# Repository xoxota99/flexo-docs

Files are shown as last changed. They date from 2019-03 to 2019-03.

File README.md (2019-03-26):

# flexo-docs

<table><tr><td width="100"></td><td>
Flexo is a 6DOF robot arm using stepper motors instead of (e.g.) servos. <br/>
This project is the documentation repository for Flexo. It includes CAD files, assembly instructions, inverse kinematics solver in Excel, datasheets, BOM, schematics, and othe miscellany that don't quite qualify as "source code".
</td></tr></table>

## See also:
<ul>
  <li><a href="https://github.com/xoxota99/flexo-server">flexo-server</a> - for documentation</li>
  <li><a href="https://github.com/xoxota99/flexo-controller">flexo-controller</a> - for Arduino code</li></li>
</ul>

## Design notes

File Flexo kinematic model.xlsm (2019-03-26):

FORWARD KINAMATICS |  |  |  |  |  |  |  |  |  | INVERSE KINAMATICS
 | IN |  |  |  |  |  | OUT |  |  |  | IN
 | degrees | radians
J1 * ( -170 / 170 ) | 0.0001 | 1.745329252e-06 |  |  |  | X | 68.71814224 |  |  | X | 68.71814224 | J1 | 9.999999996e-05
J2 * ( -132 / 0 ) | -90 | -1.570796327 |  |  |  | Y | 0.0001199357837 |  |  | Y | 0.0001199357837 | J2 | -90
J3 * ( 1 / 140 ) | 1 | -1.553343034 |  |  |  | Z | 733.6105702 |  |  | Z | 733.6105702 | J3 | 1
 | 0 | 0 |  |  |  | y | -90 | -1.570796327 |  | y | -90 | J4 | -3.113901077e-10 | -3.113901077e-10 | 180
 | 0.0001 | 1.745329252e-06 |  |  |  | p | 1.0001 | 0.01745503785 |  | p | 1.0001 | J5 | 9.999727019e-05 | 9.999727019e-05 | -9.999727019e-05 |  | WRIST CONF. | "F"
 | 0 | 3.141592654 |  |  |  | r | -90.0001 | -1.570798072 |  | r | -90.0001 | J6 | 3.113598268e-10 | 3.113598268e-10 | -180 |  | QUADRANT | 1
 | DH params
 | joint | Θ | α | d | a |  | WORK FRAME |  | TOOL FRAME | CALCULATE J1 ANGLE
 | 1 | 1.745329252e-06 | -1.570796327 | 169.77 | 64.2 | X | 0 | X | 0 | J1 ∠ | 1.745329251e-06 | 9.999999996e-05
 | 2 | -1.570796327 | 0 | 0 | 305 | Y | 0 | Y | 0
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

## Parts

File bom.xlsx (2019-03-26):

BILL OF MATERIALS
PRODUCT NAME | Flexo-XP | CONTACT INFO
APPROVED BY | Phil Desrosiers | philippe.desrosiers@gmail.com
APPROVAL DATE | 2019-03-26
PART COUNT | 144
TOTAL COST | $741.03
ITEM NUMBER | ASSEMBLY | PART | MBOM Qty | PBOM Qty | PBOM UNITS | IMAGE | CATEGORY | ASSEMBLY PHASE | STATUS | SOURCE / SUPPLIER | LINK TO SUPPORTING DOC | COMMENTS | UNIT COST | TOTAL PART COST | STATUS KEY
B-1 | Base | NEMA 23 76mm | 1 | 1 | ea |  | Motor |  |  | StepperOnline.com | https://www.omc-stepperonline.com/nema-23-stepper-motor/nema-23-bipolar-19nm-269ozin-28a-32v-57x57x76mm-4wires-%CF%866mm-shaft-23hs30-2804s1.html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 |  | $28.15 | $28.15 | NOT STARTED
B-2 | Base | Turntable ring bearing, 6" | 1 | 1 | ea |  | Bearing |  |  | Amazon.com | https://www.amazon.com/dp/B073NYZMKJ |  | $14.99 | $14.99 | IN REVIEW
B-3 | Base | 20T Mod 1 6mm Spur gear | 1 | 1 | ea |  | Gear |  |  | SPI-SD | https://shop.sdp-si.com/catalog/Product.aspx?id=A_1C_2MYK10018# |  | $7.70 | $7.70 | COMPLETE
B-4 | Base | Magnetic Encoder / Axial Magnet | 1 | 6 | ea |  | Electronics |  |  | DigiKey | https://www.digikey.com/product-detail/en/ams/AS5048A-TS_EK_AB/AS5048A-AB-1.0-ND/3188612 |  | $16.76 | $100.56 | IN PRODUCTION
B-5 | Base | M5x25mm Flat Hex screws | 2 | 1 | 50-pk |  | Fasteners |  |  | McMaster-Carr |  | Motor mount |  | $0.00
B-5 | Base | M5x25mm Button-head Hex screws | 2 | 1 | 50-pk |  | Fasteners |  |  | McMaster-Carr |  | Motor mount |  | $0.00
B-6 | Base | M8x30mm Button-head Hex screws | 4 | 1 | 50-pk |  | Fasteners |  |  | McMaster-Carr |  | Baseplate mount |  | $0.00
B-7 | Base | M5 NyLock nuts | 4 | 1 | 50-pk |  | Fasteners |  |  | McMaster-Carr |  | Motor mount |  | $0.00
B-8 | Base | M4x25mm Flat Hex screws | 8 | 1 | 50-pk |  | Fasteners |  |  | McMaster-Carr |  | Ring bearing mount |  | $0.00
BX-1 | Base | 3D-printed Housing | 1 | 1 | ea |  | 3DPrint |  |  | Internal |  |  |  | $0.00
 | Base Total |  | 25 | 15 |  |  |  |  |  |  |  |  |  | $151.40
S-1 | Shoulder | NEMA-23 47:1 Geared Motor | 1 | 2 | ea |  | Motor |  |  | StepperOnline.com | https://www.omc-stepperonline.com/nema-23-stepper-motor-bipolar-l56mm-w-gear-raio-471-planetary-gearbox-23hs22-2804s-pg47.html |  | $68.86 | $137.72
S-2 | Shoulder | 80T Mod 1 Internal Gear | 1 | 1 | ea |  | Gear |  |  | SPI-SD | http://shop.sdp-si.com/catalog/product/?id=S1E10ZM10S080 |  | $80.44 | $80.44
S-3 | Shoulder | Magnetic Encoder / Axial Magnet | 1 |  | ea |  | Electronics |  |  | DigiKey | https://www.digikey.com/product-detail/en/ams/AS5048A-TS_EK_AB/AS5048A-AB-1.0-ND/3188612 |  | $16.76 | $0.00
S-4 | Shoulder | 60x78x10mm Bearing | 1 | 4 | ea |  | Bearing |  |  | Amazon.com | https://www.amazon.com/dp/B007HS1I5E |  | $24.01 | $96.04
S-5 | Shoulder | M5x20mm Button-head Hex screws | 4 |  | 50-pk |  | Fasteners |  |  | McMaster-Carr |  | Motor mount |  | $0.00
SX-1 | Shoulder | 3D-printed Base Housing | 1 | 1 | ea |  | 3DPrint |  |  | Internal |  |  |  | $0.00
SX-2 | Shoulder | 3D-printed Loft Housing | 1 | 1 | ea |  | 3DPrint |  |  | Internal |  |  |  | $0.00
SX-5 | Shoulder | 3D-printed Bearing slip-ring | 1 | 1 | ea |  | 3DPrint |  |  | Internal |  |  |  | $0.00
 | Shoulder Total |  | 11 | 10 |  |  |  |  |  |  |  |  |  | $314.20
U-1 | Upper Arm | Steel Tubing | 1 | 1 | 10-pk |  | Structure |  |  | Amazon.com | https://www.amazon.com/gp/product/B00TH3LSJS |  | $26.70 | $26.70
U-2 | Upper Arm | 12mm Hub | 2 | 1 | 2-pk |  | Structure |  |  | Amazon.com | https://www.amazon.com/gp/product/B07J4XY6X3 |  | $12.99 | $12.99
U-3 | Upper Arm | 60x78x10mm Bearing | 2 |  | ea |  | Bearing |  |  | Amazon.com | https://www.amazon.com/dp/B007HS1I5E |  | $24.01 | $0.00
U-4 | Upper Arm | M3x12mm Button-head Hex screws | 10 | 1 | 50-pk |  | Fasteners |  |  | McMaster-Carr |  | Backplate mounting screws |  | $0.00
U-5 | Upper Arm | M3x16mm Button-head Hex screws | 4 | 1 | 50-pk |  | Fasteners |  |  | McMaster-Carr |  | Frontplate mounting screws |  | $0.00
UX-1 | Upper Arm | 3D-printed Housing, Front-Bottom | 1 | 1 | ea |  | 3DPrint |  |  | Internal |  |  |  | $0.00
UX-2 | Upper Arm | 3D-printed Housing, Back-Bottom | 1 | 1 | ea |  | 3DPrint |  |  | Internal |  |  |  | $0.00
UX-3 | Upper Arm | 3D-printed Housing, Front-Top | 1 | 1 | ea |  | 3DPrint |  |  | Internal |  |  |  | $0.00
UX-4 | Upper Arm | 3D-printed Housing, Back-Top | 1 | 1 | ea |  | 3DPrint |  |  | Internal |  |  |  | $0.00
UX-5 | Upper Arm | 3D-printed Bearing slip-ring | 2 | 2 | ea |  | 3DPrint |  |  | Internal |  |  |  | $0.00
 | Upper Arm Total |  | 25 | 10 |  |  |  |  |  |  |  |  |  | $39.69
F-1 | Forearm | NEMA-23 47:1 Geared Motor | 1 |  | ea |  | Motor |  |  | StepperOnline.com | https://www.omc-stepperonline.com/nema-23-stepper-motor-bipolar-l56mm-w-gear-raio-471-planetary-gearbox-23hs22-2804s-pg47.html |  | $68.86 | $0.00
F-2 | Forearm | NEMA-17 60mm | 2 | 3 | ea |  | Motor |  |  | StepperOnline.com | https://www.omc-stepperonline.com/nema-17-stepper-motor/nema-17-bipolar-18deg-65ncm-92ozin-21a-336v-42x42x60mm-4-wires-17hs24-2104s.html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 |  | $12.93 | $38.79
F-3 | Forearm | Magnetic Encoder / Axial Magnet | 3 |  | ea |  | Electronics |  |  | DigiKey | https://www.digikey.com/product-detail/en/ams/AS5048A-TS_EK_AB/AS5048A-AB-1.0-ND/3188612 |  | $16.76 | $0.00
F-4 | Forearm | 60x78x10mm Bearing | 1 |  | ea |  | Bearing |  |  | Amazon.com | https://www.amazon.com/dp/B007HS1I5E |  | $24.01 | $0.00
F-5 | Forearm | M5x20mm Button-head Hex screws | 4 |  | 50-pk |  | Fasteners |  |  | McMaster-Carr |  | NEMA-23 motor mounts |  | $0.00
F-6 | Forearm | M3x20mm Button-head Hex screws | 8 |  | 50-pk |  | Fasteners |  |  | McMaster-Carr |  | Housing co-mount (M3/M4/M5) |  | $0.00
F-7 | Forearm | M3x12mm Button-head Hex screws | 8 |  | 50-pk |  | Fasteners |  |  | McMaster-Carr |  | NEMA-17 motor mounts |  | $0.00
F-8 | Forearm | M3x16mm Button-head hex screws | 8 |  | 50-pk |  | Fasteners |  |  | McMaster-Carr |  | 10mm Hub mounts |  | $0.00
F-9 | Forearm | M3x10mm Button-head hex screws | 8 |  | 50-pk |  | Fasteners |  |  | McMaster-Carr |  | Access panel mounting screws |  | $0.00
F-10 | Forearm | 10x24x7mm Bearing | 2 | 2 | ea |  | Bearing |  |  | Boca Bearings | https://www.bocabearings.com/products/mr2410-zzc-2400 |  | $6.27 | $12.54
F-11 | Forearm | 8x10x236mm pipe shaft | 1 | 1 | ea |  | Motor |  |  | Amazon.com | https://www.amazon.com/dp/B07KV2JCYL |  | $24.73 | $24.73
F-12 | Forearm | 5x300mm shaft | 1 | 1 | 2-pk |  | Motor |  |  | Amazon.com | https://www.amazon.com/dp/B07KJ8DGF3 |  | $9.99 | $9.99
F-13 | Forearm | M4 Drive kit |  | 1 | ea |  | GT2 |  |  | Amazon.com | https://www.amazon.com/gp/product/B01N9EEW97 |  | $13.88 | $13.88
F-13.1 | Forearm | GT2 timing belt 200mm | 1 |  | ea
F-13.2 | Forearm | GT2 16T 5mmx6mm gear | 1 |  | ea
F-13.3 | Forearm | GT2 60T 5mmx6mm gear | 1 |  | ea |  |  |  |  |  |  | Bore out to 10mm
F-14 | Forearm | 5x8x5mm flanged sleeve bearing | 2 | 2 | ea |  | Bearing |  |  | McMaster-Carr | https://www.mcmaster.com/6659k66 |  | $1.82 | $3.64
F-15 | Forearm | 5mm/5mm shaft coupling | 1 | 1 | ea |  | Motor |  |  | Amazon.com | https://www.amazon.com/dp/B06WWR1P99 |  | $6.87 | $6.87
FX-1 | Forearm | 3D-printed Bearing slip-ring | 1 | 1 | ea |  | 3DPrint |  |  | Internal |  |  |  | $0.00
 | Forearm Total |  | 54 | 12 |  |  |  |  |  |  |  |  |  | $110.44
W-1 | Wrist | NEMA-17 Motor | 1 |  | ea |  | Motor |  |  | StepperOnline.com | https://www.omc-stepperonline.com/nema-17-stepper-motor/nema-17-bipolar-18deg-65ncm-92ozin-21a-336v-42x42x60mm-4-wires-17hs24-2104s.html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 |  | $12.93 | $0.00
W-2 | Wrist | Magnetic Encoder / Axial Magnet | 1 |  | ea |  | Electronics |  |  | DigiKey | https://www.digikey.com/product-detail/en/ams/AS5048A-TS_EK_AB/AS5048A-AB-1.0-ND/3188612 |  | $16.76 | $0.00
W-3 | Wrist | GT2 30T 5x6mm Gear | 1 | 1 | ea |  | GT2 |  |  | Amazon.com | https://www.amazon.com/uxcell-Aluminum-Timing-Synchronous-Printer/dp/B0728PDWNQ |  | $6.41 | $6.41
W-4 | Wrist | GT2 50T 5x6mm Gear | 1 | 1 | ea |  | GT2 |  |  | Amazon.com | https://www.amazon.com/dp/B07FMX1PTY |  | $11.44 | $11.44
W-5 | Wrist | GT2 Timing belt ???mm | 1 | 1 | ea |  | GT2 |  |  | SDP-SD |  |  |  | $0.00
W-6 | Wrist | GT2 Idler 3x14mm | 4 | 1 | 5-pk |  | GT2 |  |  | Amazon.com | https://www.amazon.com/dp/B01N2TQNGW |  | $5.99 | $5.99
W-7 | Wrist | Bearing 16x30x7mm | 1 | 1 | ea |  | Bearing |  |  | Boca Bearings | https://www.bocabearings.com/products/os160-th9-c3c-2953 |  | $12.57 | $12.57
W-8 | Wrist | Bearing 5x8x5 | 1 | 1 | ea |  | Bearing |  |  | Boca Bearings | https://www.bocabearings.com/products/mr85-w5c-15184 |  | $6.97 | $6.97
W-10 | Wrist | 5mm Hub | 1 | 1 | 2-pk |  | Structure |  |  | Pololu | https://www.pololu.com/product/1998 |  | $7.49 | $7.49
WX-1 | Wrist | 3D-printed Housing, Bracket | 1 |  |  |  | 3D Print |  |  | Internal |  |  |  | $0.00
WX-2 | Wrist | 3D-printed Housing, M6 Mount | 1 |  |  |  | 3D Print |  |  | Internal |  |  |  | $0.00
WX-3 | Wrist | 3D-printed Housing, Idler spacer | 1 |  |  |  | 3D Print |  |  | Internal |  |  |  | $0.00
WX-4 | Wrist | 3D-printed Housing, Knuckle | 1 |  |  |  | 3D Print |  |  | Internal |  |  |  | $0.00
 | Wrist Total |  | 16 | 7 |  |  |  |  |  |  |  |  |  | $50.87
G-1 | Gripper | rack & pinion bearings | 4 | 1 | 8-pk |  |  |  |  |  | https://www.amazon.com/gp/product/B07M9VNCY5 |  | $22.09 | $22.09
G-2 | Gripper | rack & pinion rails | 1 | 1 | 20-pk |  |  |  |  |  | https://www.amazon.com/gp/product/B00OK6DT76 |  | $9.02 | $9.02
G-3 | Gripper | Servo | 1 | 1 | ea |  |  |  |  |  | https://www.amazon.com/gp/product/B0006O3XKO |  | $43.32 | $43.32
GX-1 | Gripper | 3D-printed servo mount | 1 |  |  |  | 3D Print |  |  | Internal |  |  |  | $0.00
GX-2 | Gripper | 3D-printed linkage | 2 |  |  |  | 3D Print |  |  | Internal |  |  |  | $0.00
GX-3 | Gripper | 3D-printed finger | 2 |  |  |  | 3D Print |  |  | Internal |  |  |  | $0.00
GX-4 | Gripper | 3D-printed rack endcap | 2 |  |  |  | 3D Print |  |  | Internal |  |  |  | $0.00
 | Gripper Total |  | 13 | 3 |  |  |  |  |  |  |  |  |  | $74.43
 | Grand Total |  | 144 | 57 |  |  |  |  |  |  |  |  |  | $741.03

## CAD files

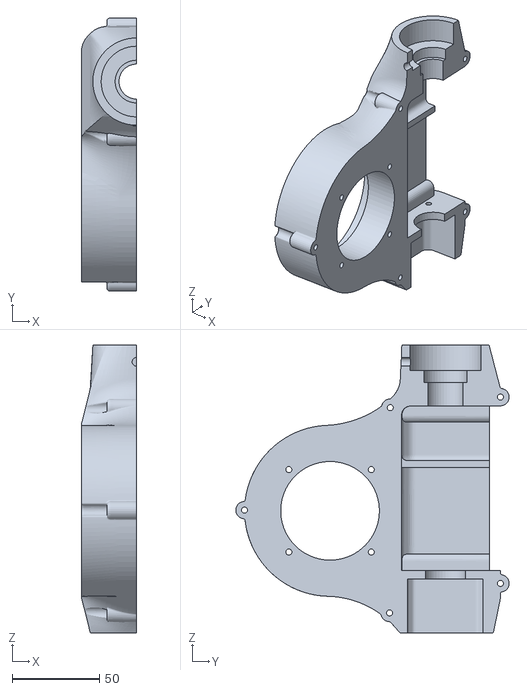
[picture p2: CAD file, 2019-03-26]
CAD/XP-Forearm-M3-Right.stl
31.5 x 156.6 x 165.0

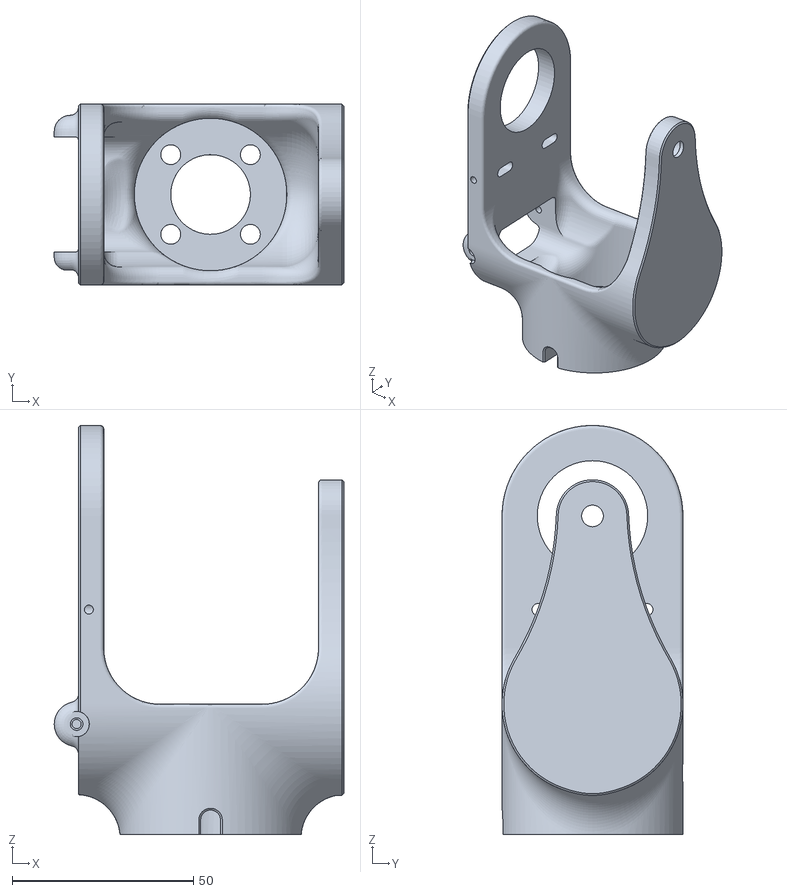
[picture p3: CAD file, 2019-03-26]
CAD/XP-Wrist-Bracket.stl
80.0 x 50.0 x 113.0

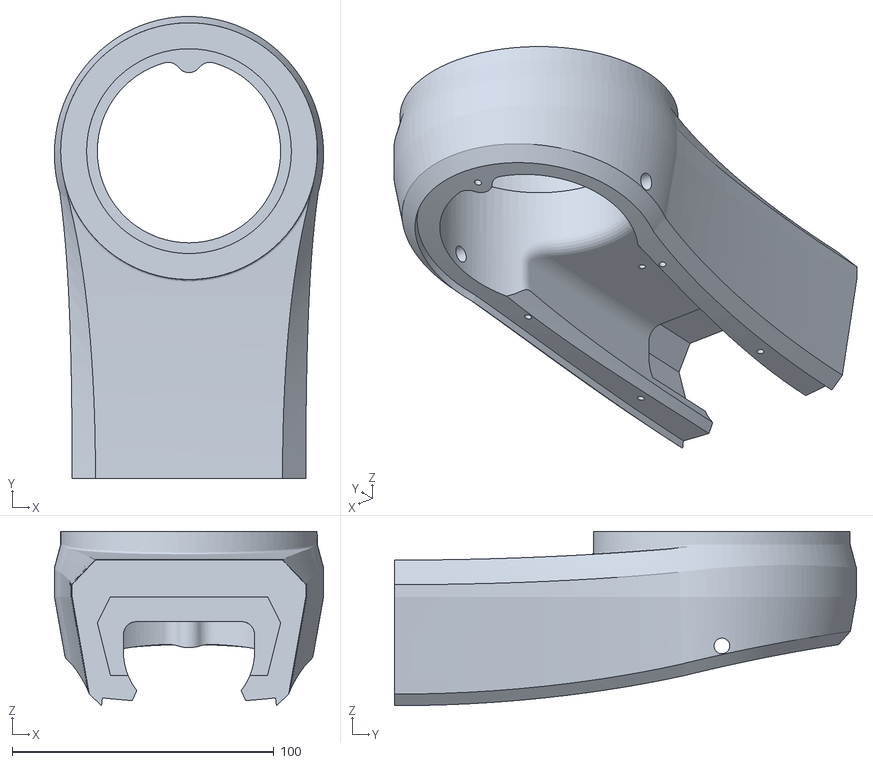
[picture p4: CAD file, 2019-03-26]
CAD/XP-Bicep-Housing-Top.stl
102.8 x 176.4 x 66.6

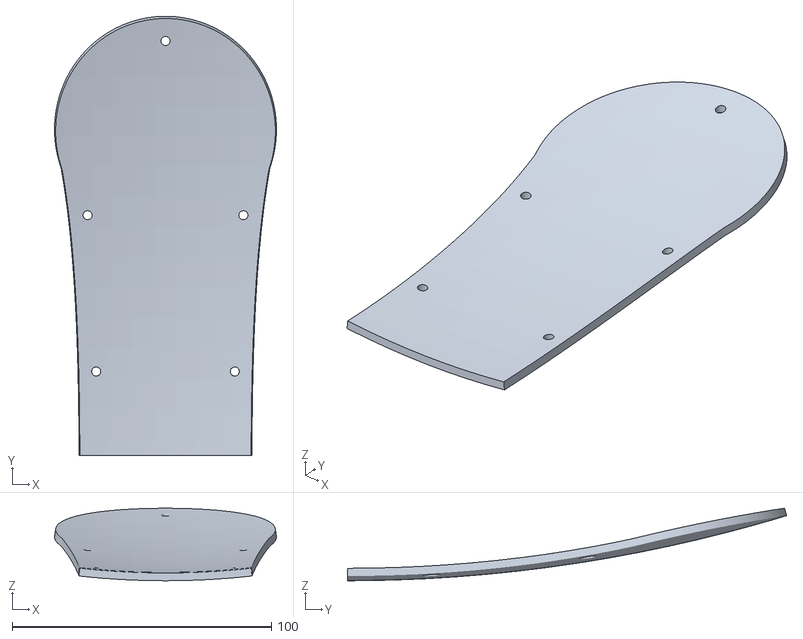
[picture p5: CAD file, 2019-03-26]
CAD/XP-Bicep-Backplate-Top.stl
85.7 x 169.6 x 28.0

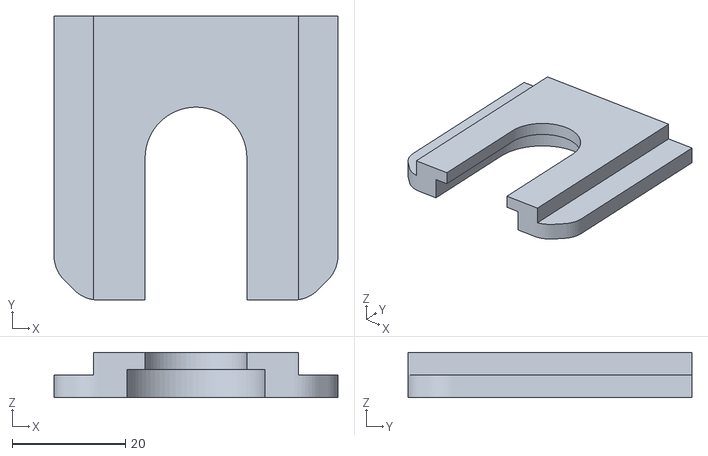
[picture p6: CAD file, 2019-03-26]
CAD/XP-Forearm-M5-Bearing-Holder.stl
50.2 x 50.2 x 8.00

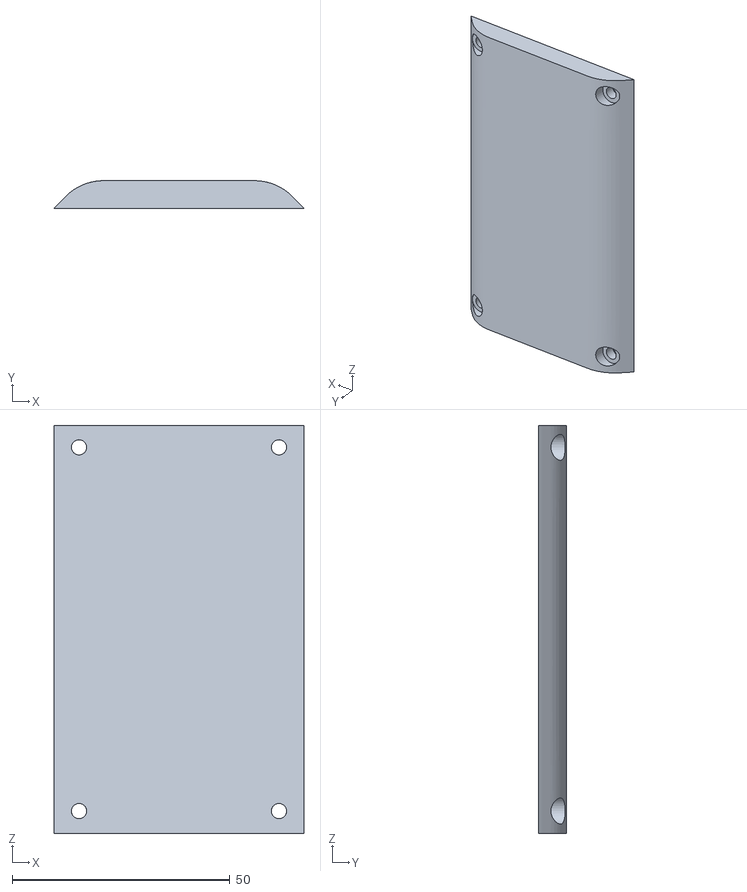
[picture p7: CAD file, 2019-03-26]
CAD/XP-Forearm-M5-Panel.stl
57.4 x 6.38 x 93.8

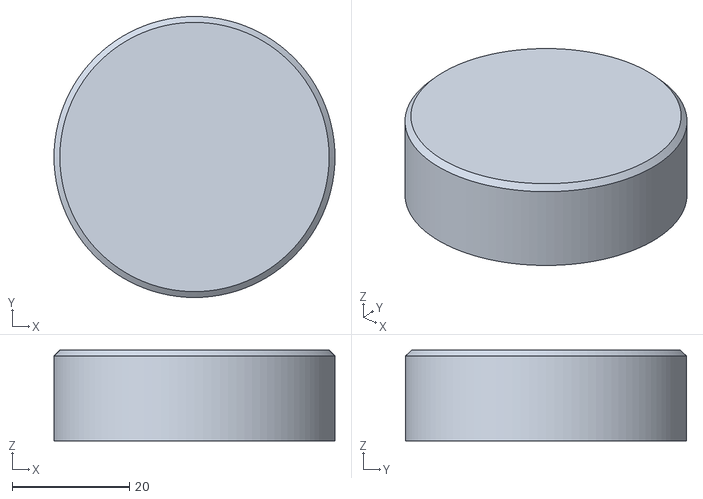
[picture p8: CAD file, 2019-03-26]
CAD/XP-Wrist-Knuckle.stl
48.0 x 48.0 x 15.5

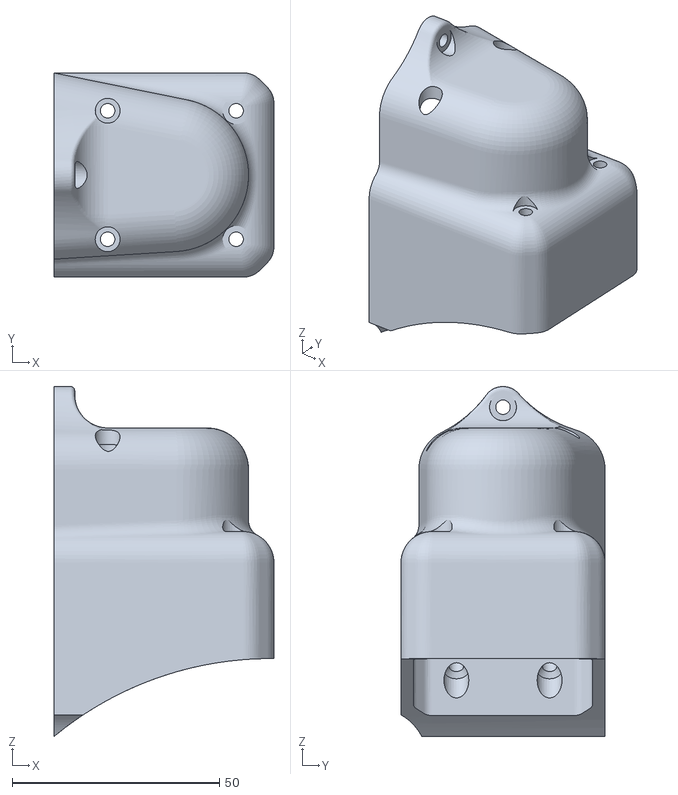
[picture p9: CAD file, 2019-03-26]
CAD/XP-Forearm-M4.stl
53.1 x 49.2 x 84.5

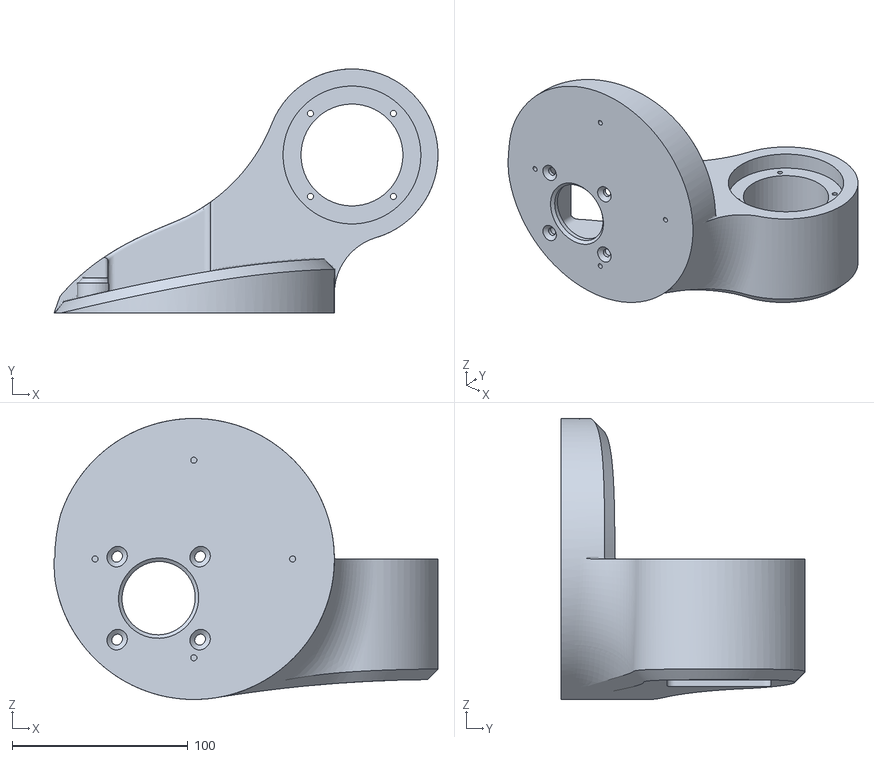
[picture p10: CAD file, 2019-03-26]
CAD/XP-Shoulder.stl
218.6 x 139.0 x 160.0

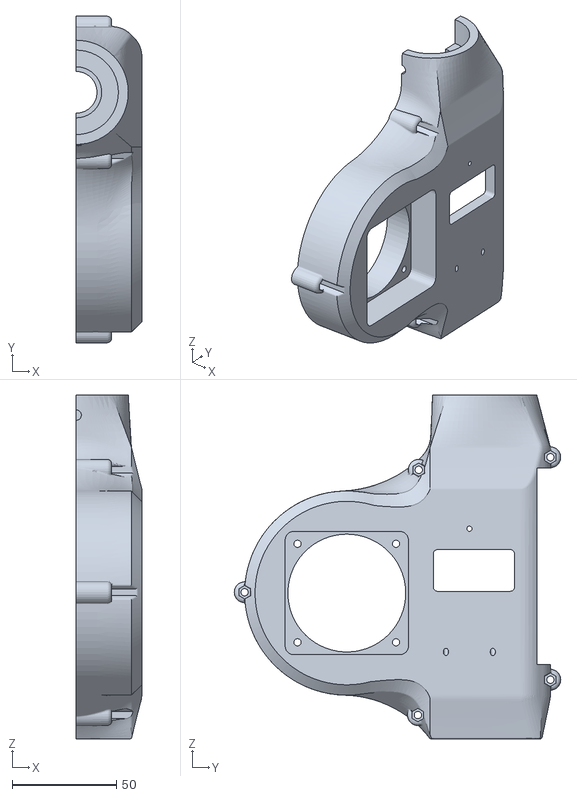
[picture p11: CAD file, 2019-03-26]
CAD/XP-Forearm-M3-Left.stl
31.5 x 156.6 x 165.0

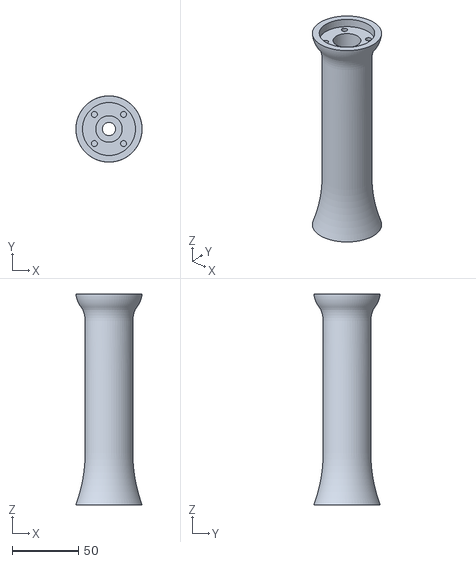
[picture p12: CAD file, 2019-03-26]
CAD/XP-Forearm-Shaft.stl
50.0 x 50.0 x 159.1

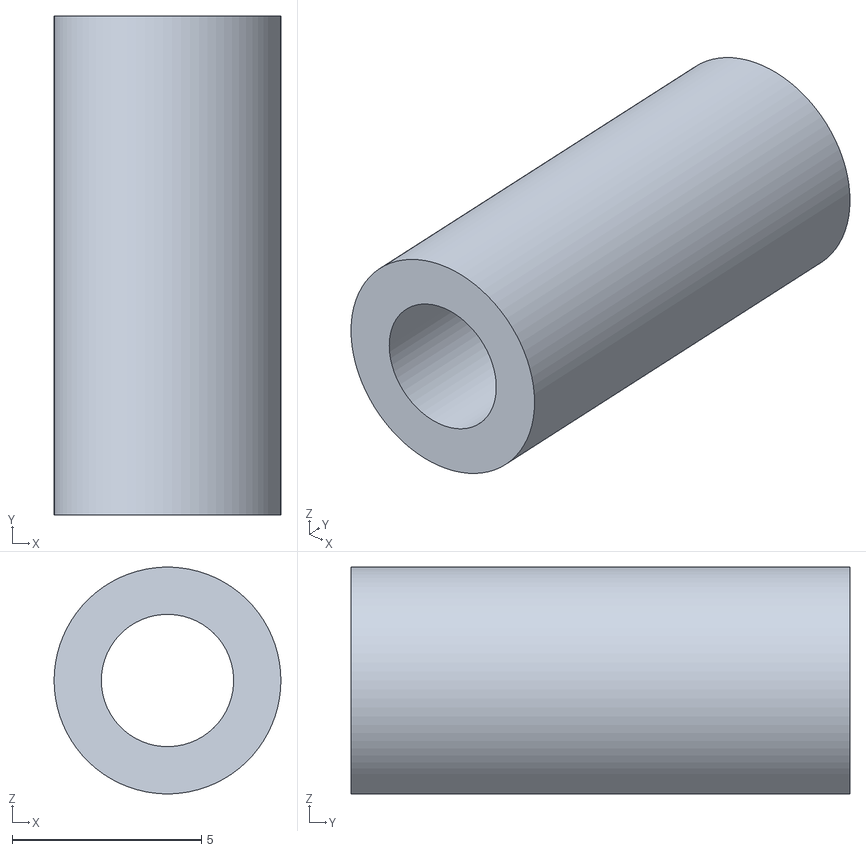
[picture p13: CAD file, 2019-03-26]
CAD/XP-Wrist-Spacer.stl
6.00 x 13.2 x 6.00

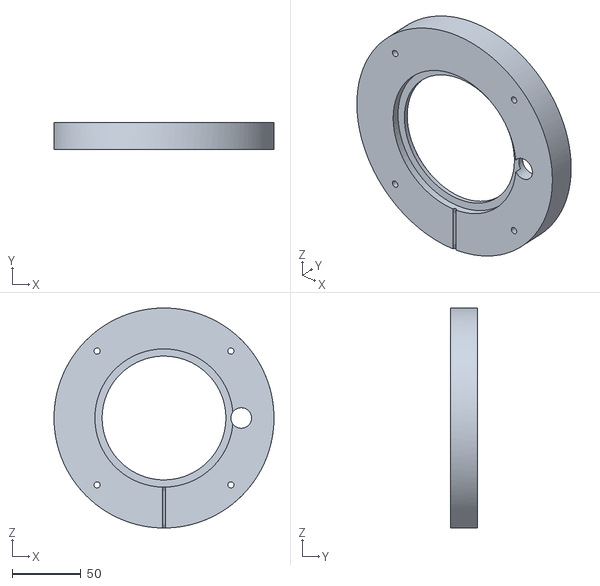
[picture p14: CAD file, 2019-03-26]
CAD/XP-Base-Top.stl
160.0 x 19.8 x 160.0

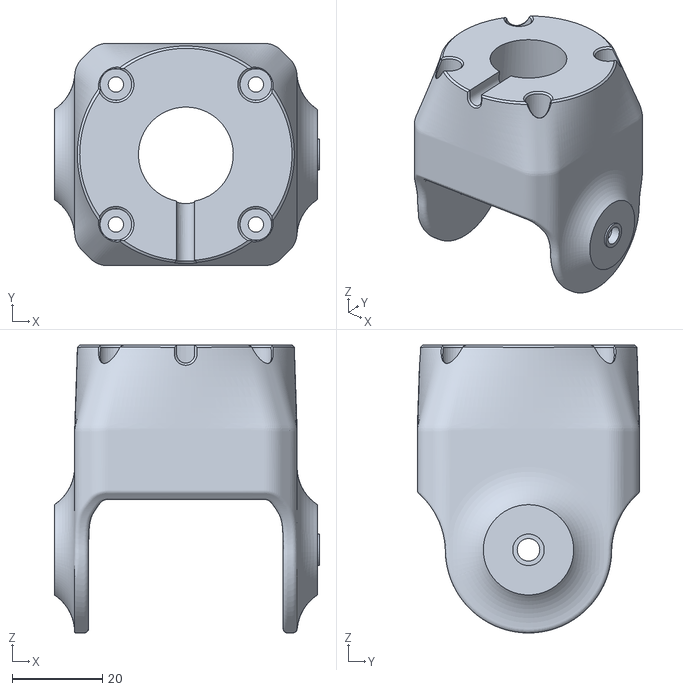
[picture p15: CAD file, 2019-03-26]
CAD/XP-Wrist-M6-Housing.stl
58.8 x 49.2 x 63.8

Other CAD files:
CAD/XP-Bicep-Backplate-Bottom.stl
CAD/XP-Bicep-Housing-Bottom.stl
CAD/XP-Base-Bottom.stl
CAD/XP-Bicep-Insert.stl

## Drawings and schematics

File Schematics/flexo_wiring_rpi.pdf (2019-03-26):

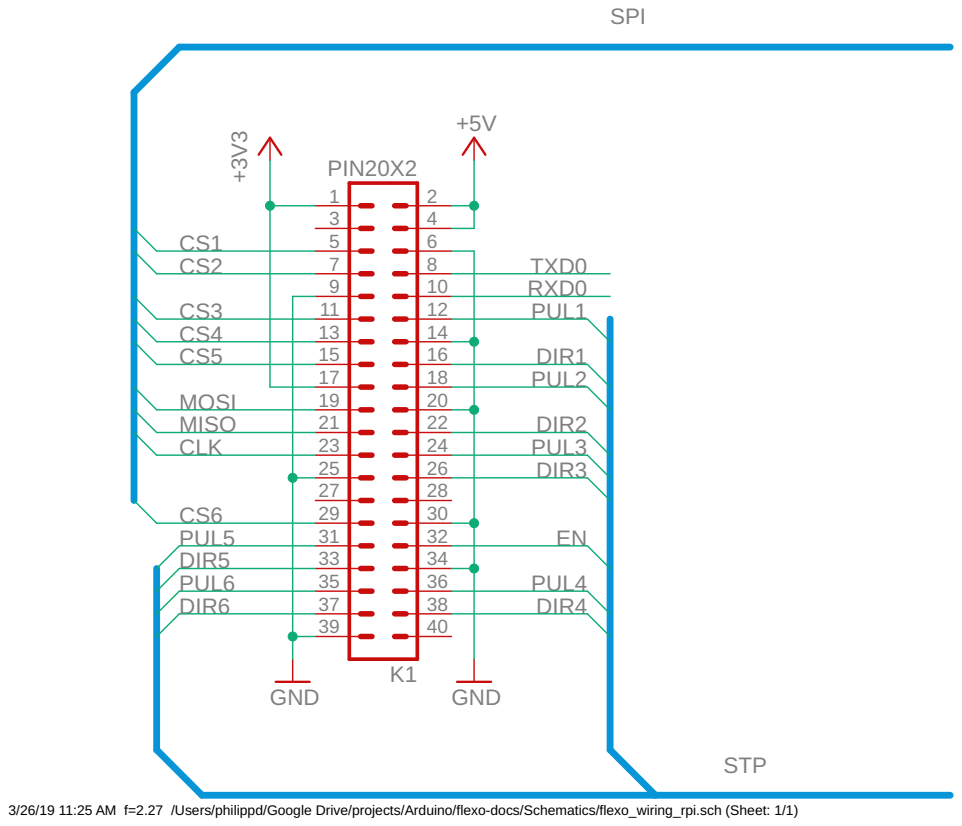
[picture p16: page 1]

3/26/19 11:25 AM f=2.27 /Users/philippd/Google Drive/projects/Arduino/flexo-docs/Schematics/flexo_wiring_rpi.sch (Sheet: 1/1)

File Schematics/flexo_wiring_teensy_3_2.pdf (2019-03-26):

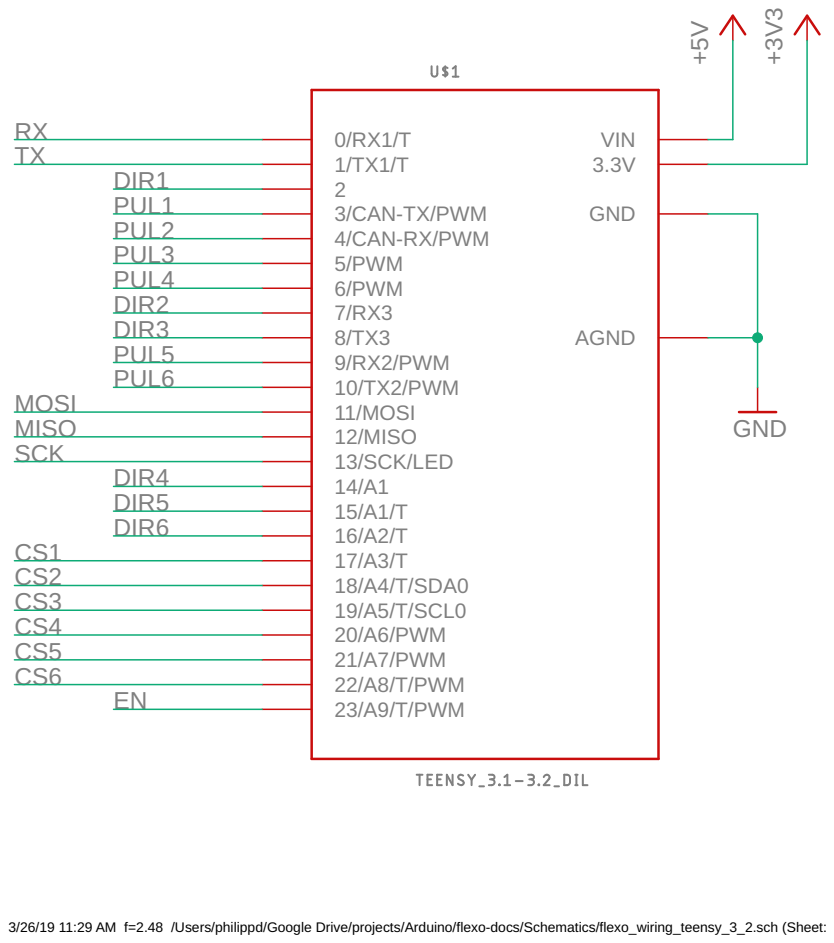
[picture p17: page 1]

3/26/19 11:29 AM f=2.48 /Users/philippd/Google Drive/projects/Arduino/flexo-docs/Schematics/flexo_wiring_teensy_3_2.sch (Sheet: 1/1)
